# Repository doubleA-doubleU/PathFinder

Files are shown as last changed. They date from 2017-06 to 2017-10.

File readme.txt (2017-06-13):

PathFinder Line-Following Differential Drive Robot

Android phone (Samsung Galaxy S5)
Microchip PIC32MX250F128B microcontroller
Custom PCB with mounting holes for:
	28 Pin DIP socket
	Mini USB connector
	Slideswitch
	MCP1702 voltage regulator (TO92)
	3mm red LED with 330 Ohm resistor
	Reset button with 10 kOhm resistor
	3mm green LED with 330 Ohm resistor
	User button with 10 kOhm resistor
	8 MHz crystal resonator
	4x 0.1 uF capacitors
	2x 10 uF polarized capacitors
	5-pin breakout for PICkit3 programmer
	2x 8-pin breakouts for remaining I/O pins and power/ground connections
2x 12V N20 DC motor w/ 298:1 gearhead (running on 5V from phone)
2x brass hex head (12.5mm) motor coupler with set screws
Towerpro SG90 micro servo
DRV8835 H-bridge https://www.pololu.com/product/2135
HTC Vive Position Sensor (TS3633-CM1) https://www.triadsemi.com/product/ts3633-cm1/
3D printed:
	Chassis
	2x wheels
	2x motor mounts
	Caster socket
5/8 inch ball bearing
4x M3x10mm bolts w/ hex nuts and washers
2x M4x10mm bolts
1x M3x20mm bolt w/ hex nut and washer
2x 2 inch o-rings
Elastic band to hold phone in place
USB OTG cable (micro to mini)

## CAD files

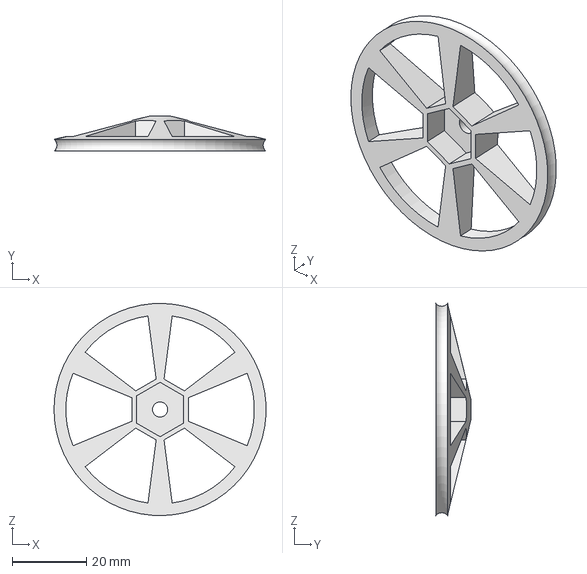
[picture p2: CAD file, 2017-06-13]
Parts/wheel.FCStd
57.1 x 9.53 x 57.1 mm

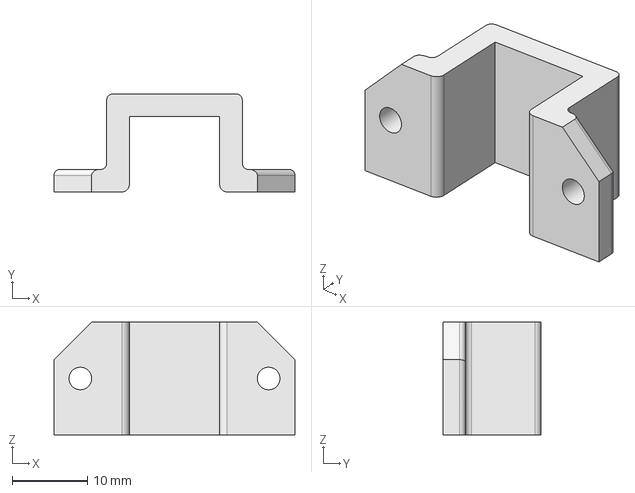
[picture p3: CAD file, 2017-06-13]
Parts/motor_mount.FCStd
32.0 x 13.0 x 15.0 mm

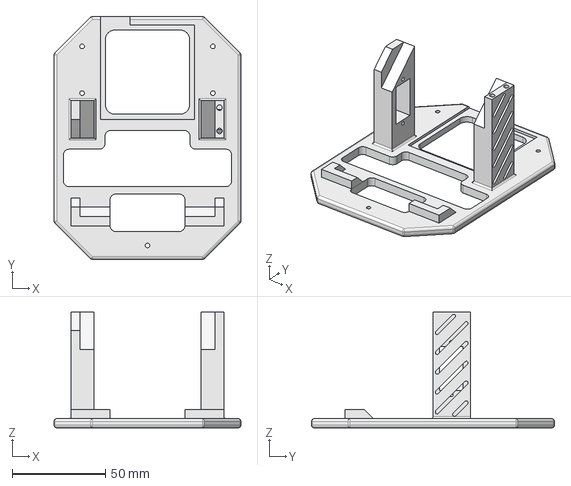
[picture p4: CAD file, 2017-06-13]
Parts/chassis.FCStd
100.0 x 130.0 x 62.0 mm

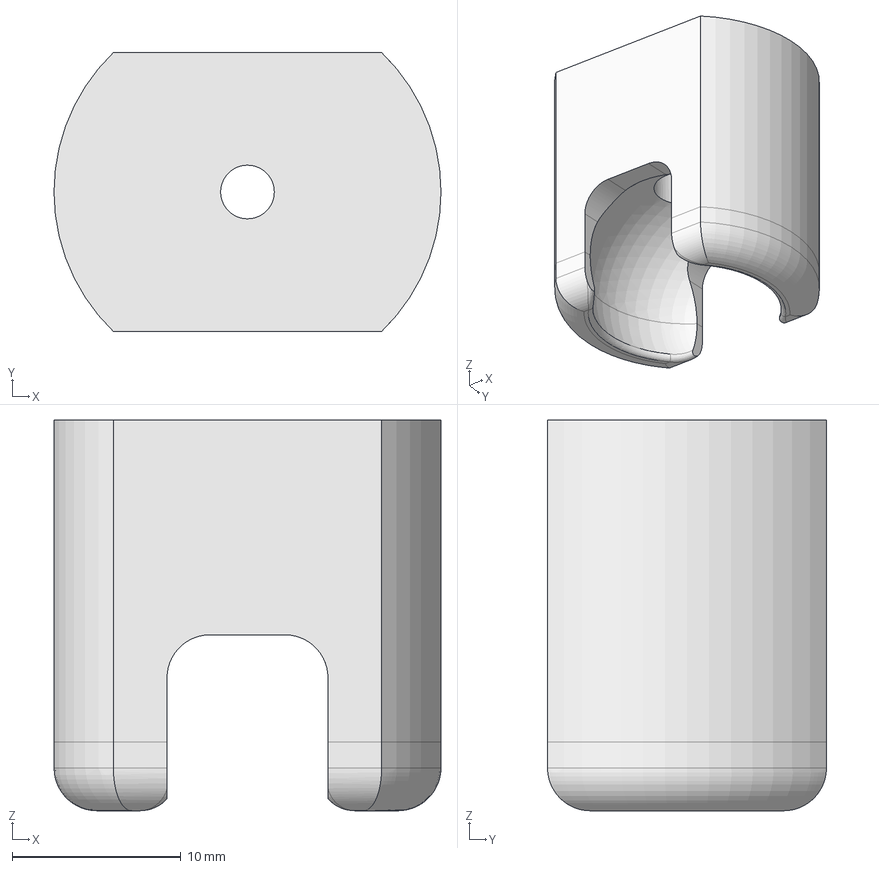
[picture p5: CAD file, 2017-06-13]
Parts/caster.FCStd
22.9 x 16.5 x 23.1 mm

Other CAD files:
Parts/caster.stl
Parts/chassis.stl
Parts/motor_mount.stl
Parts/wheel.stl

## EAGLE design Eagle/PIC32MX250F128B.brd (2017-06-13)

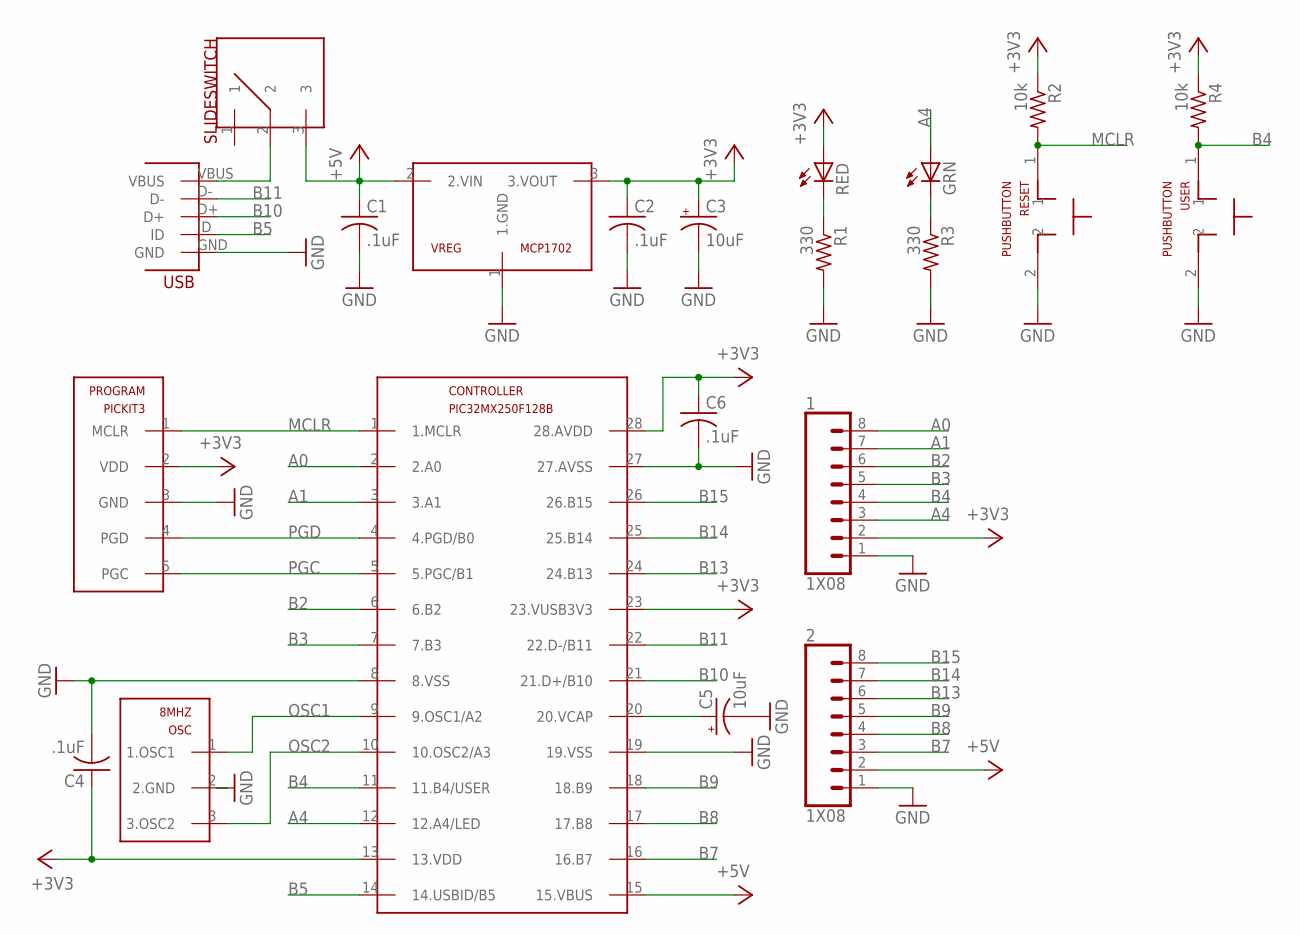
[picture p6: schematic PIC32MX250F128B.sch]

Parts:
1, 2: 1X08; CONN_08
8MHZ: OSC
C1, C2, C4, C6: .1uF; C025-025X050
C3, C5: 10uF; B45181B
CONTROLLER: PIC32MX250F128B; DIL28-3
GRN: LED3MM
PROGRAM: PICKIT3
R1, R3: 330; 0207/10
R2, R4: 10k; 0207/10
RED: LED3MM
RESET: PUSHBUTTON
SLIDESWITCH: SLIDESWITCH
USB: MINIUSB; USB-MB-H
USER: PUSHBUTTON
VREG: MCP1702; TO92

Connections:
+3V3: 1.2, C2.1, C3.+, C4.1, C6.1, CONTROLLER.13 (13.VDD), CONTROLLER.23 (23.VUSB3V3), CONTROLLER.28 (28.AVDD), PROGRAM.2 (VDD), R2.1, R4.1, RED.A, VREG.3 (3.VOUT)
+5V: 2.2, C1.1, CONTROLLER.15 (15.VBUS), SLIDESWITCH.3, VREG.2 (2.VIN)
A0: 1.8, CONTROLLER.2 (2.A0)
A1: 1.7, CONTROLLER.3 (3.A1)
A4: 1.3, CONTROLLER.12 (12.A4/LED), GRN.A
B2: 1.6, CONTROLLER.6 (6.B2)
B3: 1.5, CONTROLLER.7 (7.B3)
B4: 1.4, CONTROLLER.11 (11.B4/USER), R4.2, USER.1
B5: CONTROLLER.14 (14.USBID/B5), USB.ID
B7: 2.3, CONTROLLER.16 (16.B7)
B8: 2.4, CONTROLLER.17 (17.B8)
B9: 2.5, CONTROLLER.18 (18.B9)
B10: CONTROLLER.21 (21.D+/B10), USB.D+
B11: CONTROLLER.22 (22.D-/B11), USB.D-
B13: 2.6, CONTROLLER.24 (24.B13)
B14: 2.7, CONTROLLER.25 (25.B14)
B15: 2.8, CONTROLLER.26 (26.B15)
GND: 1.1, 2.1, 8MHZ.2 (2.GND), C1.2, C2.2, C3.-, C4.2, C5.-, C6.2, CONTROLLER.8 (8.VSS), CONTROLLER.19 (19.VSS), CONTROLLER.27 (27.AVSS), PROGRAM.3 (GND), R1.2, R3.2, RESET.2, USB.GND, USER.2, VREG.1 (1.GND)
MCLR: CONTROLLER.1 (1.MCLR), PROGRAM.1 (MCLR), R2.2, RESET.1
unnamed: R1.1, RED.K (C)
unnamed: GRN.K (C), R3.1
OSC1: 8MHZ.1 (1.OSC1), CONTROLLER.9 (9.OSC1/A2)
OSC2: 8MHZ.3 (3.OSC2), CONTROLLER.10 (10.OSC2/A3)
PGC: CONTROLLER.5 (5.PGC/B1), PROGRAM.5 (PGC)
PGD: CONTROLLER.4 (4.PGD/B0), PROGRAM.4 (PGD)
VBUS: SLIDESWITCH.2, USB.VBUS
VCAP: C5.+, CONTROLLER.20 (20.VCAP)

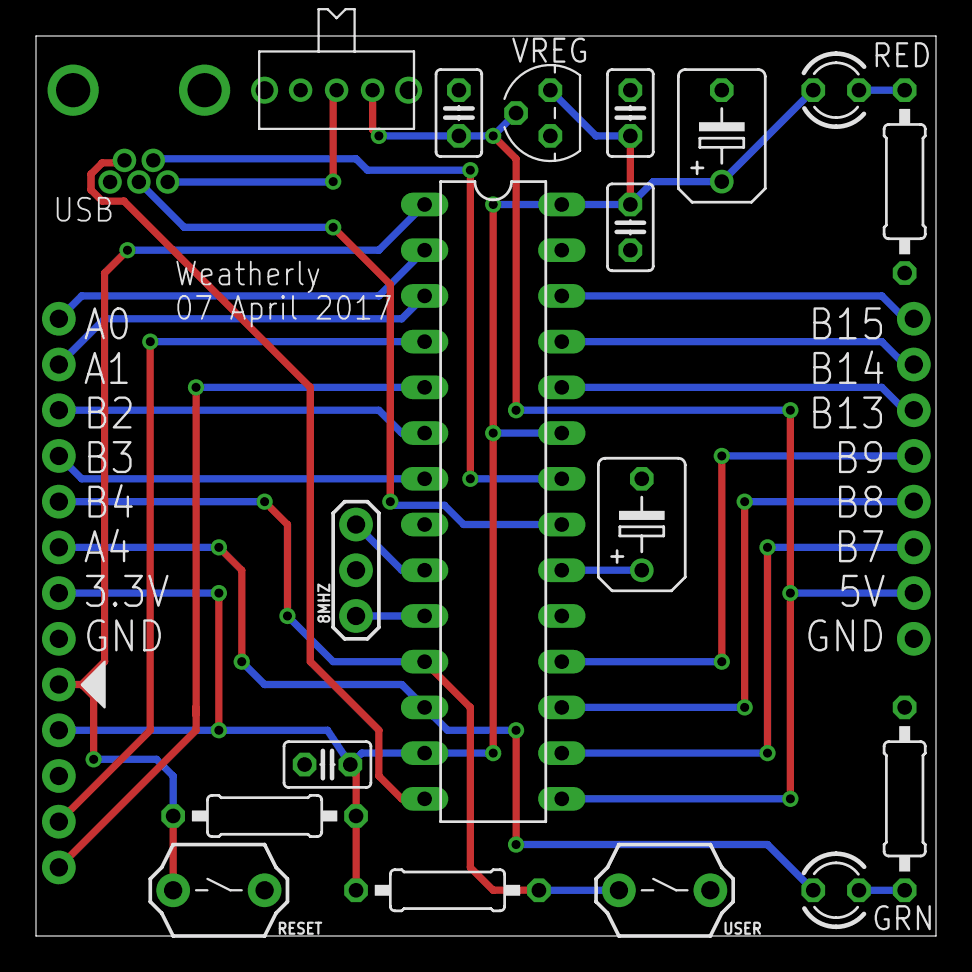
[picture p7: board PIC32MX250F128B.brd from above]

Board: 2 copper layers, 50.0 x 50.0 mm, 22 parts (0 on the bottom side), 27 nets.

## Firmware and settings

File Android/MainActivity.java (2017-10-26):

package com.example.aaron.pathfinder;

// libraries

import android.Manifest;
import android.app.Activity;
import android.app.PendingIntent;
import android.content.Context;
import android.content.Intent;
import android.content.pm.PackageManager;
import android.graphics.Bitmap;
import android.graphics.Canvas;
import android.graphics.Paint;
import android.graphics.SurfaceTexture;
import android.hardware.Camera;
import android.hardware.usb.UsbDeviceConnection;
import android.hardware.usb.UsbManager;
import android.os.Bundle;
import android.support.v4.app.ActivityCompat;
import android.support.v4.content.ContextCompat;
import android.view.SurfaceHolder;
import android.view.SurfaceView;
import android.view.TextureView;
import android.view.View;
import android.view.WindowManager;
import android.widget.Button;
import android.widget.TextView;
import android.widget.SeekBar;
import android.widget.SeekBar.OnSeekBarChangeListener;

import com.hoho.android.usbserial.driver.CdcAcmSerialDriver;
import com.hoho.android.usbserial.driver.ProbeTable;
import com.hoho.android.usbserial.driver.UsbSerialDriver;
import com.hoho.android.usbserial.driver.UsbSerialPort;
import com.hoho.android.usbserial.driver.UsbSerialProber;
import com.hoho.android.usbserial.util.SerialInputOutputManager;

import java.io.IOException;
import java.io.UnsupportedEncodingException;
import java.util.List;
import java.util.concurrent.ExecutorService;
import java.util.concurrent.Executors;

import static android.graphics.Color.blue;
import static android.graphics.Color.green;
import static android.graphics.Color.red;
import static android.graphics.Color.rgb;

public class MainActivity extends Activity implements TextureView.SurfaceTextureListener {
    private Camera mCamera;
    private TextureView mTextureView;
    private SurfaceView mSurfaceView;
    private SurfaceHolder mSurfaceHolder;
    private Bitmap bmp = Bitmap.createBitmap(640, 480, Bitmap.Config.ARGB_8888);
    private Canvas canvas = new Canvas(bmp);
    private Paint paint1 = new Paint();
    private TextView myTextView;
    private TextView myTextView2;
    private TextView myTextView3;
    private SeekBar threshold;
    private SeekBar threshold2;
    private Button button;
    int thresh = 125;
    int thresh2 = 300;
    int go = 0;

    private UsbManager manager;
    private UsbSerialPort sPort;
    private final ExecutorService mExecutor = Executors.newSingleThreadExecutor();
    private SerialInputOutputManager mSerialIoManager;

    protected void onCreate(Bundle savedInstanceState) {
        super.onCreate(savedInstanceState);
        setContentView(R.layout.activity_main);
        getWindow().addFlags(WindowManager.LayoutParams.FLAG_KEEP_SCREEN_ON); // keeps the screen from turning off

        threshold = (SeekBar) findViewById(R.id.seek1);
        threshold2 = (SeekBar) findViewById(R.id.seek2);
        myTextView = (TextView) findViewById(R.id.textView01);
        myTextView2 = (TextView) findViewById(R.id.textView02);
        myTextView3 = (TextView) findViewById(R.id.textView03);
        button = (Button) findViewById(R.id.button1);

        button.setOnClickListener(new View.OnClickListener() {
            @Override
            public void onClick(View v) { // change state variable
                go = go + 1;
                if (go > 1) {
                    go = 0;
                    // send 641 to the PIC to stop motors (outside of expected range for COM)
                    int temp = 641;
                    String sendString = String.valueOf(temp) + '\n';
                    for (int j = 0; j < 3; j++) { // send multiple times to make sure the robot "hears" it
                        try {
                            sPort.write(sendString.getBytes(), 10); // 10 is the timeout
                        } catch (IOException e) {
                        }
                    }
                }
            }
        });

        // see if the app has permission to use the camera
        //ActivityCompat.requestPermissions(MainActivity.this, new String[]{Manifest.permission.CAMERA}, 1);
        if (ContextCompat.checkSelfPermission(this, Manifest.permission.CAMERA) == PackageManager.PERMISSION_GRANTED) {
            mSurfaceView = (SurfaceView) findViewById(R.id.surfaceview);
            mSurfaceHolder = mSurfaceView.getHolder();

            mTextureView = (TextureView) findViewById(R.id.textureview);
            mTextureView.setSurfaceTextureListener(this);

            // set the paintbrush for writing text on the image
            paint1.setColor(0xffff0000); // red
            paint1.setTextSize(24);
        }

        setMyControlListener();
        manager = (UsbManager) getSystemService(Context.USB_SERVICE);
    }

    public void onSurfaceTextureAvailable(SurfaceTexture surface, int width, int height) {
        mCamera = Camera.open(); // might crash here if native camera app is running
        Camera.Parameters parameters = mCamera.getParameters();
        parameters.setPreviewSize(640, 480);
        parameters.setFocusMode(Camera.Parameters.FOCUS_MODE_INFINITY); // no autofocusing
        parameters.setAutoExposureLock(false); // auto exposure is on
        mCamera.setParameters(parameters);
        mCamera.setDisplayOrientation(90); // rotate to portrait mode

        try {
            mCamera.setPreviewTexture(surface);
            mCamera.startPreview();
        } catch (IOException ioe) {
            // Something bad happened
        }
    }

    public void onSurfaceTextureSizeChanged(SurfaceTexture surface, int width, int height) {
        // Ignored, Camera does all the work for us
    }

    public boolean onSurfaceTextureDestroyed(SurfaceTexture surface) {
        mCamera.stopPreview();
        mCamera.release();
        return true;
    }

    // SeekBars
    private void setMyControlListener() {
        threshold.setOnSeekBarChangeListener(new OnSeekBarChangeListener() {

            @Override
            public void onProgressChanged(SeekBar seekBar, int progress, boolean fromUser) {
                thresh = progress;
                myTextView.setText("Blue Greater Than: "+thresh);
            }

            @Override
            public void onStartTrackingTouch(SeekBar seekBar) {
            }

            @Override
            public void onStopTrackingTouch(SeekBar seekBar) {
            }
        });
        threshold2.setOnSeekBarChangeListener(new OnSeekBarChangeListener() {
            @Override
            public void onProgressChanged(SeekBar seekBar, int progress, boolean fromUser) {
                thresh2 = progress;
                myTextView2.setText("Start Y: "+thresh2);
            }

            @Override
            public void onStartTrackingTouch(SeekBar seekBar) {
            }

            @Override
            public void onStopTrackingTouch(SeekBar seekBar) {
            }
        });
    }

    // USB functionality
    private final SerialInputOutputManager.Listener mListener =
            new SerialInputOutputManager.Listener() {
                @Override
                public void onRunError(Exception e) {

                }

                @Override
                public void onNewData(final byte[] data) {
                    MainActivity.this.runOnUiThread(new Runnable() {
                        @Override
                        public void run() {
                            MainActivity.this.updateReceivedData(data);
                        }
                    });
                }
            };

    @Override
    protected void onPause(){
        super.onPause();
        stopIoManager();
        if(sPort != null){
            try{
                sPort.close();
            } catch (IOException e){ }
            sPort = null;
        }
        finish();
    }

    @Override
    protected void onResume() {
        super.onResume();

        ProbeTable customTable = new ProbeTable();
        customTable.addProduct(0x04D8,0x000A, CdcAcmSerialDriver.class);
        UsbSerialProber prober = new UsbSerialProber(customTable);

        final List<UsbSerialDriver> availableDrivers = prober.findAllDrivers(manager);

        if(availableDrivers.isEmpty()) {
            //check
            return;
        }

        UsbSerialDriver driver = availableDrivers.get(0);
        sPort = driver.getPorts().get(0);

        if (sPort == null){
            //check
        }else{
            final UsbManager usbManager = (UsbManager) getSystemService(Context.USB_SERVICE);
            UsbDeviceConnection connection = usbManager.openDevice(driver.getDevice());
            if (connection == null){
                //check
                PendingIntent pi = PendingIntent.getBroadcast(this, 0, new Intent("com.android.example.USB_PERMISSION"), 0);
                usbManager.requestPermission(driver.getDevice(), pi);
                return;
            }

            try {
                sPort.open(connection);
                sPort.setParameters(9600, 8, UsbSerialPort.STOPBITS_1, UsbSerialPort.PARITY_NONE);

            }catch (IOException e) {
                //check
                try{
                    sPort.close();
                } catch (IOException e1) { }
                sPort = null;
                return;
            }
        }
        onDeviceStateChange();
    }

    private void stopIoManager(){
        if(mSerialIoManager != null) {
            mSerialIoManager.stop();
            mSerialIoManager = null;
        }
    }

    private void startIoManager() {
        if(sPort != null){
            mSerialIoManager = new SerialInputOutputManager(sPort, mListener);
            mExecutor.submit(mSerialIoManager);
        }
    }

    private void onDeviceStateChange(){
        stopIoManager();
        startIoManager();
    }

    private void updateReceivedData(byte[] data) {
        //do something with received data

        //for displaying:
        if (go ==1) {
            String rxString = null;
            try {
                rxString = new String(data, "UTF-8"); // put the data you got into a string
                myTextView3.setText(rxString);
            } catch (UnsupportedEncodingException e) {
                e.printStackTrace();
            }
        }
    }

    // the important function
    public void onSurfaceTextureUpdated(SurfaceTexture surface) {
        if (go == 1) {
            int M = 0;
            int sum = 0;
            int COM;
            // every time there is a new Camera preview frame
            mTextureView.getBitmap(bmp);

            final Canvas c = mSurfaceHolder.lockCanvas();
            if (c != null) {
                int[] pixels = new int[bmp.getWidth()]; // pixels[] is the RGBA data

                int startY = thresh2; // which row in the bitmap to analyze to read
                bmp.getPixels(pixels, 0, bmp.getWidth(), 0, startY, bmp.getWidth(), 1);
                // in the row, see if the pixel is grey or brown
                for (int i = 0; i < bmp.getWidth(); i++) {
                    if (blue(pixels[i]) > thresh) {
                        pixels[i] = rgb(0, 255, 0); // over write the pixel with pure green
                        // COM pixel calculation
                        M = M + 1;
                        sum = sum + i;
                    }
                }
                // update the row
                bmp.setPixels(pixels, 0, bmp.getWidth(), 0, startY, bmp.getWidth(), 1);

                // draw a circle at COM
                if (M == 0) {
                    COM = 0;
                } else {
                    COM = (sum / M) + 1;
                }
                canvas.drawCircle(COM, startY, 5, paint1); // x position, y position, diameter, color

                // write the COM as text
                canvas.drawText("COM = " + COM, 10, 30, paint1);

                //send COM to PIC
                String sendString = String.valueOf(COM) + '\n';
                try {
                    sPort.write(sendString.getBytes(), 10); // 10 is the timeout
                } catch (IOException e) {}
            }
            c.drawBitmap(bmp, 0, 0, null);
            mSurfaceHolder.unlockCanvasAndPost(c);
        }
    }
}

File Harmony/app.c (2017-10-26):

/*******************************************************************************
  MPLAB Harmony Application Source File
  
  Company:
    Microchip Technology Inc.
  
  File Name:
    app.c

  Summary:
    This file contains the source code for the MPLAB Harmony application.

  Description:
    This file contains the source code for the MPLAB Harmony application.  It 
    implements the logic of the application's state machine and it may call 
    API routines of other MPLAB Harmony modules in the system, such as drivers,
    system services, and middleware.  However, it does not call any of the
    system interfaces (such as the "Initialize" and "Tasks" functions) of any of
    the modules in the system or make any assumptions about when those functions
    are called.  That is the responsibility of the configuration-specific system
    files.
 *******************************************************************************/

// DOM-IGNORE-BEGIN
/*******************************************************************************
Copyright (c) 2013-2014 released Microchip Technology Inc.  All rights reserved.

Microchip licenses to you the right to use, modify, copy and distribute
Software only when embedded on a Microchip microcontroller or digital signal
controller that is integrated into your product or third party product
(pursuant to the sublicense terms in the accompanying license agreement).

You should refer to the license agreement accompanying this Software for
additional information regarding your rights and obligations.

SOFTWARE AND DOCUMENTATION ARE PROVIDED "AS IS" WITHOUT WARRANTY OF ANY KIND,
EITHER EXPRESS OR IMPLIED, INCLUDING WITHOUT LIMITATION, ANY WARRANTY OF
MERCHANTABILITY, TITLE, NON-INFRINGEMENT AND FITNESS FOR A PARTICULAR PURPOSE.
IN NO EVENT SHALL MICROCHIP OR ITS LICENSORS BE LIABLE OR OBLIGATED UNDER
CONTRACT, NEGLIGENCE, STRICT LIABILITY, CONTRIBUTION, BREACH OF WARRANTY, OR
OTHER LEGAL EQUITABLE THEORY ANY DIRECT OR INDIRECT DAMAGES OR EXPENSES
INCLUDING BUT NOT LIMITED TO ANY INCIDENTAL, SPECIAL, INDIRECT, PUNITIVE OR
CONSEQUENTIAL DAMAGES, LOST PROFITS OR LOST DATA, COST OF PROCUREMENT OF
SUBSTITUTE GOODS, TECHNOLOGY, SERVICES, OR ANY CLAIMS BY THIRD PARTIES
(INCLUDING BUT NOT LIMITED TO ANY DEFENSE THEREOF), OR OTHER SIMILAR COSTS.
 *******************************************************************************/
// DOM-IGNORE-END


// *****************************************************************************
// *****************************************************************************
// Section: Included Files 
// *****************************************************************************
// *****************************************************************************

#include "app.h"
#include <stdio.h>
#include <xc.h>
#include <math.h>

// *****************************************************************************
// *****************************************************************************
// Section: Global Data Definitions
// *****************************************************************************
// *****************************************************************************


// *****************************************************************************
/* Application Data

  Summary:
    Holds application data

  Description:
    This structure holds the application's data.

  Remarks:
    This structure should be initialized by the APP_Initialize function.
    
    Application strings and buffers are be defined outside this structure.
 */

APP_DATA appData;

// *****************************************************************************
// *****************************************************************************
// Section: Application Callback Functions
// *****************************************************************************
// *****************************************************************************

/* TODO:  Add any necessary callback functions.
 */

/*******************************************************
 * USB CDC Device Events - Application Event Handler
 *******************************************************/

USB_DEVICE_CDC_EVENT_RESPONSE APP_USBDeviceCDCEventHandler
(
        USB_DEVICE_CDC_INDEX index,
        USB_DEVICE_CDC_EVENT event,
        void * pData,
        uintptr_t userData
        ) {
    APP_DATA * appDataObject;
    appDataObject = (APP_DATA *) userData;
    USB_CDC_CONTROL_LINE_STATE * controlLineStateData;

    switch (event) {
        case USB_DEVICE_CDC_EVENT_GET_LINE_CODING:

            /* This means the host wants to know the current line
             * coding. This is a control transfer request. Use the
             * USB_DEVICE_ControlSend() function to send the data to
             * host.  */

            USB_DEVICE_ControlSend(appDataObject->deviceHandle,
                    &appDataObject->getLineCodingData, sizeof (USB_CDC_LINE_CODING));

            break;

        case USB_DEVICE_CDC_EVENT_SET_LINE_CODING:

            /* This means the host wants to set the line coding.
             * This is a control transfer request. Use the
             * USB_DEVICE_ControlReceive() function to receive the
             * data from the host */

            USB_DEVICE_ControlReceive(appDataObject->deviceHandle,
                    &appDataObject->setLineCodingData, sizeof (USB_CDC_LINE_CODING));

            break;

        case USB_DEVICE_CDC_EVENT_SET_CONTROL_LINE_STATE:

            /* This means the host is setting the control line state.
             * Read the control line state. We will accept this request
             * for now. */

            controlLineStateData = (USB_CDC_CONTROL_LINE_STATE *) pData;
            appDataObject->controlLineStateData.dtr = controlLineStateData->dtr;
            appDataObject->controlLineStateData.carrier = controlLineStateData->carrier;

            USB_DEVICE_ControlStatus(appDataObject->deviceHandle, USB_DEVICE_CONTROL_STATUS_OK);

            break;

        case USB_DEVICE_CDC_EVENT_SEND_BREAK:

            /* This means that the host is requesting that a break of the
             * specified duration be sent. Read the break duration */

            appDataObject->breakData = ((USB_DEVICE_CDC_EVENT_DATA_SEND_BREAK *) pData)->breakDuration;

            /* Complete the control transfer by sending a ZLP  */
            USB_DEVICE_ControlStatus(appDataObject->deviceHandle, USB_DEVICE_CONTROL_STATUS_OK);

            break;

        case USB_DEVICE_CDC_EVENT_READ_COMPLETE:

            /* This means that the host has sent some data*/
            appDataObject->isReadComplete = true;
            break;

        case USB_DEVICE_CDC_EVENT_CONTROL_TRANSFER_DATA_RECEIVED:

            /* The data stage of the last control transfer is
             * complete. For now we accept all the data */

            USB_DEVICE_ControlStatus(appDataObject->deviceHandle, USB_DEVICE_CONTROL_STATUS_OK);
            break;
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
